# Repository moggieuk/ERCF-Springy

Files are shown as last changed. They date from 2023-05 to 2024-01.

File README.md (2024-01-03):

# ERCF-Springy (BETA-2)

ERCF "Springy" is a modification/upgrade to the ERCF v1.1 design.  One of the problems with ERCF is tuning the grip on the filament by swapping out different sized "top-hats" until sufficent grip is found.  This is a hassle and, although mostly works, the problem is that the flexible nature of the connection of filament blocks and the fact that the servo arm wears over time means that it isn't reliable.  Enter "Springy"...

Springy is a reworked Selector Cart (and ancillary components) with built in articulated sprung servo.  The whole servo assembly moves to ensure consistent pressure to grip the filament and works with a single "universal" top-hat.

## Beta 1 -> Beta 2 Changes:
<ol>
<li>Improved supports (gaps)
<li>Adjustment screw for spring (must always use the Spring_Cap.stl part). Obviously you need to add a threaded insert at the top of the spring hole -- careful you need a steady had to do this.
<li>Minor adjustment to servo mounting carts - they had a slightly lower resting position than desired
<li>The servo pivot is no longer two screws but a single M3x20.  It makes is slightly more difficult to assembly because you need to attach the encoder at the same time as securing the pivot for the servo. Idea from ERCF discord channel.
<li>STLs Updated: `[a]_Springy_Selector_Cart.stl`, `Spring_Cap.stl`, `Springy_MG90S_Servo_Mount.stl`, `Springy_Savox_Servo_Mount.stl`
</ol>

Also check out my other ERCF projects:
<ul>
<li>Happy Hare v3 software (https://github.com/moggieuk/ERCF-Software-V3)
<li>KlipperScreen Happy Hare Edition (https://github.com/moggieuk/KlipperScreen-Happy-Hare-Edition)
</ul>

Also, some folks have asked about making a donation to cover the cost of the all the coffee I'm drinking.  I'm not doing this for any financial reward but it you feel inclined a donation to PayPal https://www.paypal.me/moggieuk will certainly be spent making your life with ERCF more enjoyable.

Thank you!

## "Springy" Internals
This cross section reveals how Spring works.  The servo (both MG90S and Savox SH255mg are supported) pivots and provides about 2-3mm of movement.  The updated servo arm design aligns with the new universal top hat and ensures constant grip with varying distances and servo arm wear.

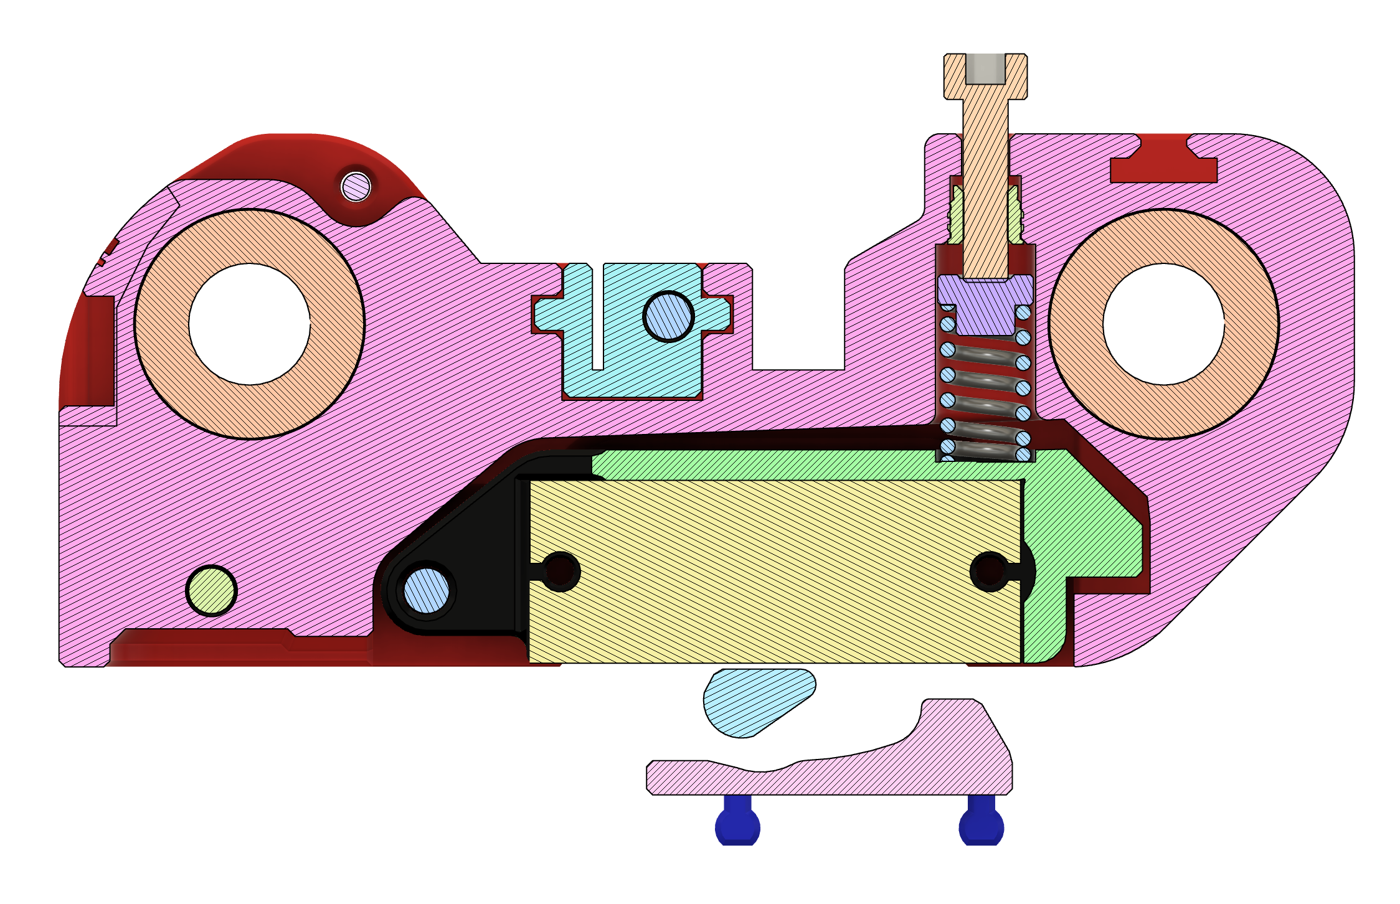
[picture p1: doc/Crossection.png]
ERCF Springy Cross Section


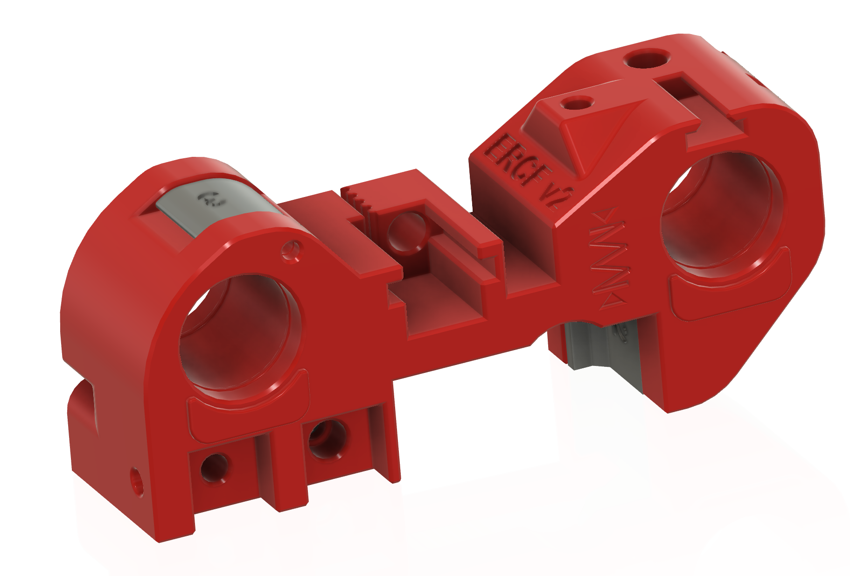
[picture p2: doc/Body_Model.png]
New Selector Arm Body


Other changes / notes:
<ul>
<li>The "Idler Block" at the end of the 8mm rods should be replaced to provide an enlarged pocket for servo movement.
<li>You must replace all your top-hats with the "universal" design supplied.
<li>The selector door has been strengthed in the hinge area and now locks with two 3x2mm magnets.
<li>Articulated servo mounts are provided for both the popular MG90S and Savox servo options.
<li>Springs from about 10mm to 15mm accomodated - cut it too long.  You do want the 1mm s/steel wire size though to provide the correct pressure.
</ul>

## Parts needed

### Printed Parts
In addition to the selector cart it is important to print and fit a new "Idler Block" to ensure the servo will not bind and wires have room to move. Also make sure you use the new top-hat and correct servo arm (the MG90S and Savox are different spline patterns!)

### Hardware
<ul>
<li>1x M3x20mm SHCS bolt for articulated servo pivot. This secures both the encoder and is the pivot for the articulated servo arm.
<li>1x 10mm - 15mm s/s compression spring.  This should be a 6mm diameter, 1mm wire compression spring.
<li>1x M3 heatset for the spring compression adjustment
<li>2x 3x2mm round neodymium magnets.  These are optional if you want the updated cover to lock shut.
<li>2x M2x8mm self tapping "servo" screws (these are the ones that were probably supplied with servo). Note the warning about too long screws below.

Here is the articulated servo mount showing the MG90S servo verion and a 12mm spring. The Savox mount is slightly different.

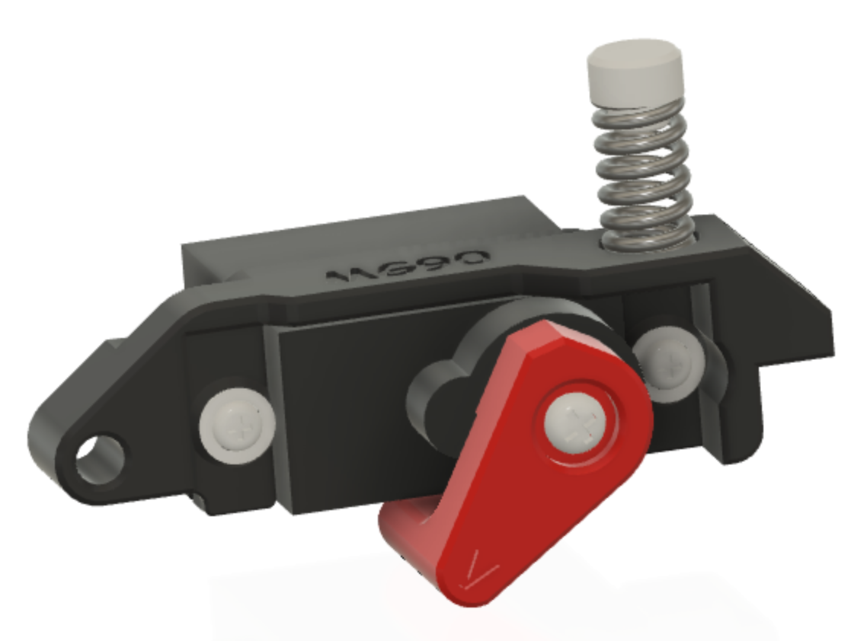
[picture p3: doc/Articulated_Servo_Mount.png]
MG90S Articulated Servo Mount


## Assembly

* Dissassembly: Remove the 6mm selector belt and separate the 8mm rods from the "Idle Block" end.  Remove the Encoder from the Selector Cart.  Remove the old Selector Cart from the 8mm rods.

* TO avoid clearance problems make sure to replace the Idle Block with the new one because is has a slightly enlarged cutout for servo.
  
* The servo mounts have break away suppports (MG90S has 4, Savox has 2) shown in grey below.  [Note: The print orientation is chosen to ensure strengh in the hinge area]. The M3 brass inserts are the same as the original with one exception.  The insert that forms the pivot for the servo should be set 1mm BELOW the surface.  The new STL has provision for this.

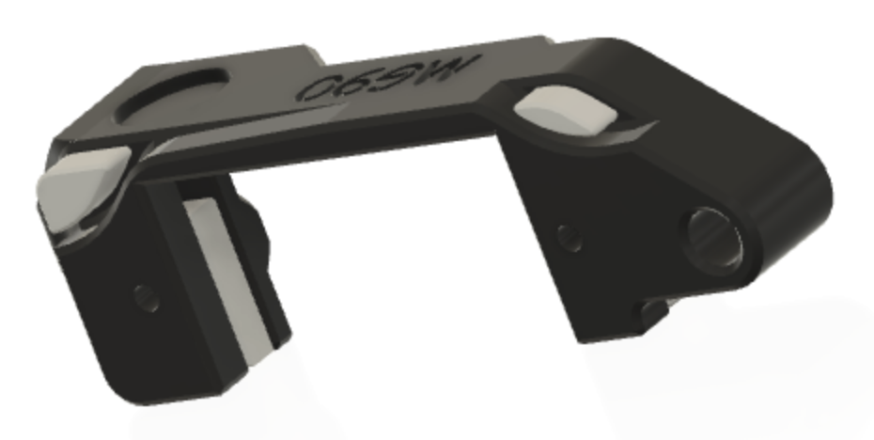
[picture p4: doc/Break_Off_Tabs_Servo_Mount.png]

  
* Fit the servo with two M2x6mm (or 8mm) self tapping screws.  IMPORTANT: Make sure the screws don't poke through to the other side. If they do, remove then and file then slightly before refitting. I found the screws supplied by the servo vendors fitted but others can be a little long.

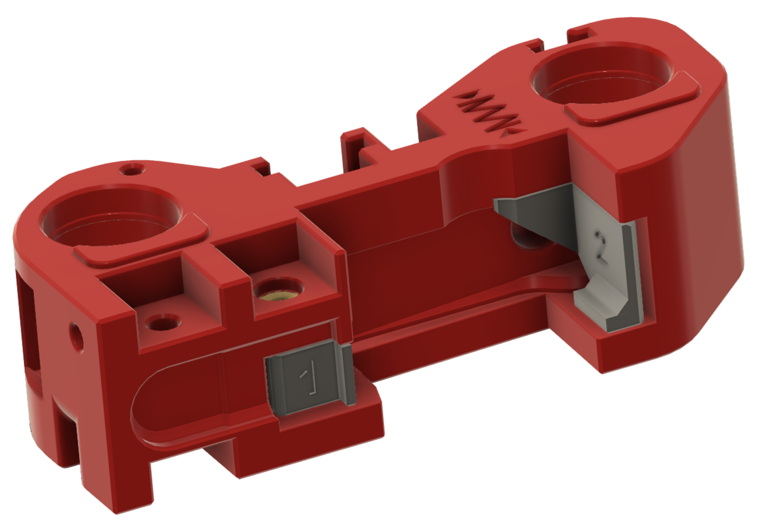
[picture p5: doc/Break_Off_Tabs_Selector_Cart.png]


* Break away the 3 numbered supports from the Selector Cart.

* Press a M3 heatset at the back of the spring hole.  Putting on the heatset on a M2 allen or small screwdriver will help guide it.  CAREFULLY with a steady hand, press the heatset into the base of the hole without deforming the surrounding plastic.

* Fit the spring and spring cap into the cart.  Insert the servo assemply spring side first then depress the pivot side and secure the servo pivot with a M3x20mm SHCS bolt (the same one that will later hold the encoder).

It should articulate similar to this video: (https://www.youtube.com/shorts/Brj2L9Y7NeA)

* Add back the encoder changing the one M3x8mm to a M3x20mm SHCS (fits into the other side of the brass insert shared with the servo pivot).
  
* Secure the servo wiring as shown in the picture.  The *small* loop will provide necessary free movement to prevent strain on the wire. **Don't fit the servo arm at this stage.**

Servo Wire 

* Reassemble ERCF and reconnect wiring.

* Replace all the Top Hats with the universal one supplied in this repo (they have a v2.0 printed on the top edge)

* Insert a 3x2mm magnet into the new stronger connector cover and corresponding hole on the selector cart
  
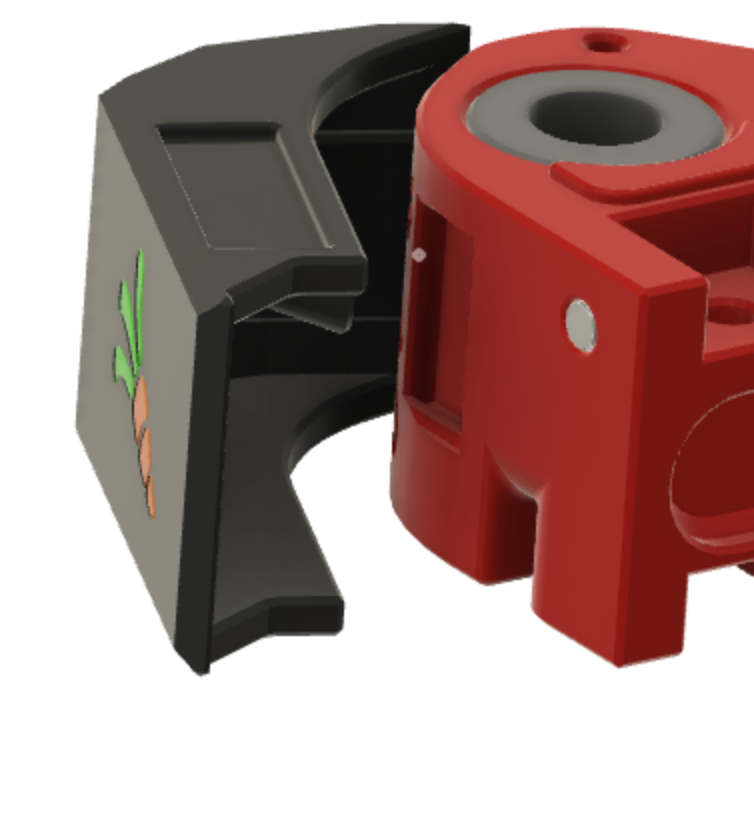
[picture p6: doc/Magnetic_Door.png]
Magnetic_Door
   

* Once ERCF is operational again, align the selector with one of the gates. Run `ERCF_SERVO_UP` to ensure the servo is in the up position.  Fit the new servo arm (Savox version has "S" on arm, MG90S is blank) on the spine that best holds the arm against the servo body (fine adjustments can be made later to the servo angle in `ercf_parameters.cfg`)

* Run `ERCF_SERVO_DOWN` or `ERCF_TEST_SERVO VALUE=xxx` to find the angle where the `V` on the servo arm aligns with the tiny `^` on the Top Hat.  This eliminates any judgement and represents the best location for the down position. **NOTE: the angle of movement is a little bit smaller than before, so don't assume your existing value is correct - test again carefully working up to the correct postion!
* For Happy Hare use:  `MMU_SERVO POS=down` or `MMU_SERVO ANGLE=xxx`

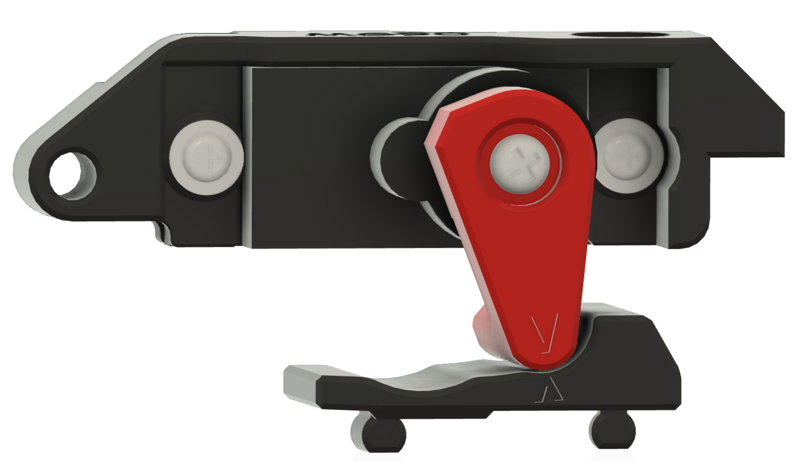
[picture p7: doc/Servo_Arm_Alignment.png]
Servo Arm Alignement


Now enjoy more reliable and hopefully less filament slippage.   Note: This removes one or two variables from your setup -- friction in the filament path can still lead to problems.

Good luck.  You can find me on Discord as `moggieuk#6538`

    (\_/)
    ( *,*)
    (")_(") ERCF Ready

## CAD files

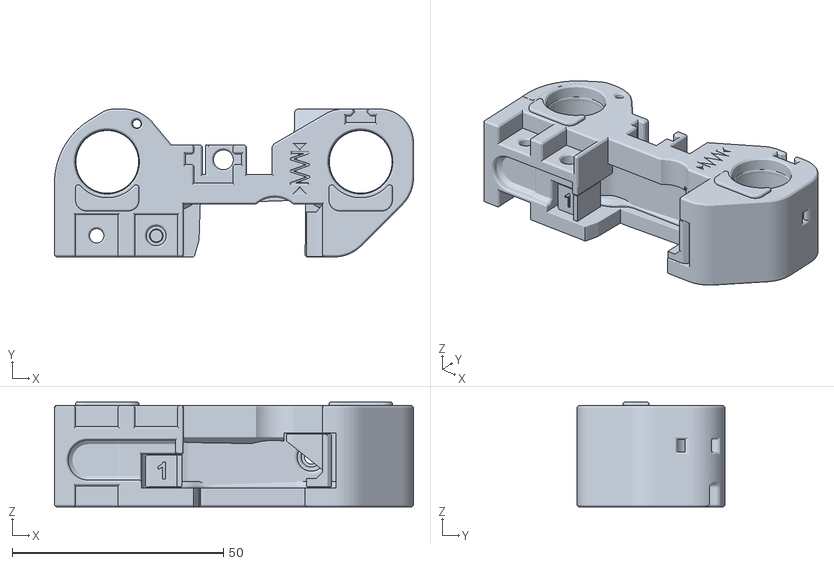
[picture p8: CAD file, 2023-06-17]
[a]_Springy_Selector_Cart.stl
85.0 x 35.0 x 24.8

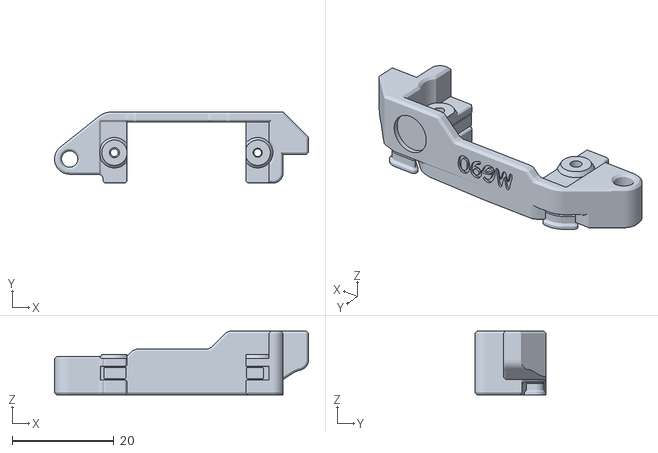
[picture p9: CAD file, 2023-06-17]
MG90S_Servo_Option/Springy_MG90S_Servo_Mount.stl
50.0 x 14.0 x 12.5

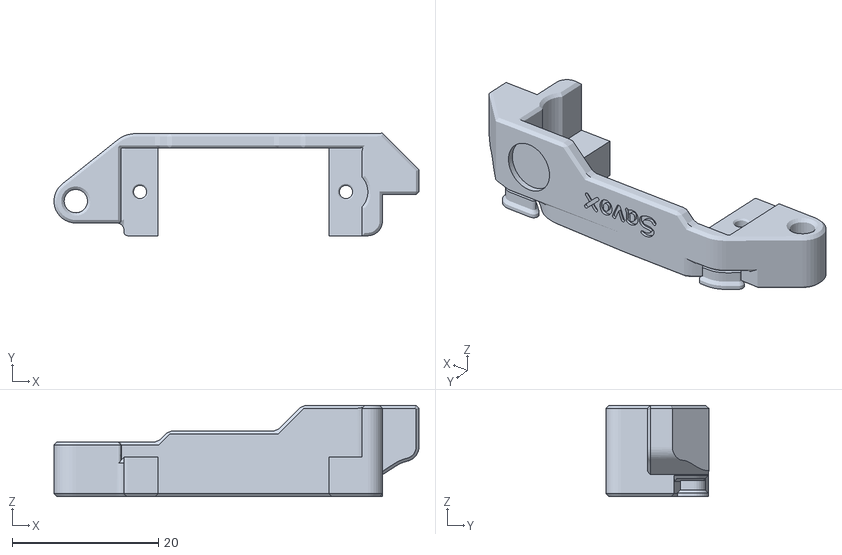
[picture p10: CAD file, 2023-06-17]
Savox_Servo_Option/Springy_Savox_Servo_Mount.stl
50.0 x 14.0 x 12.5

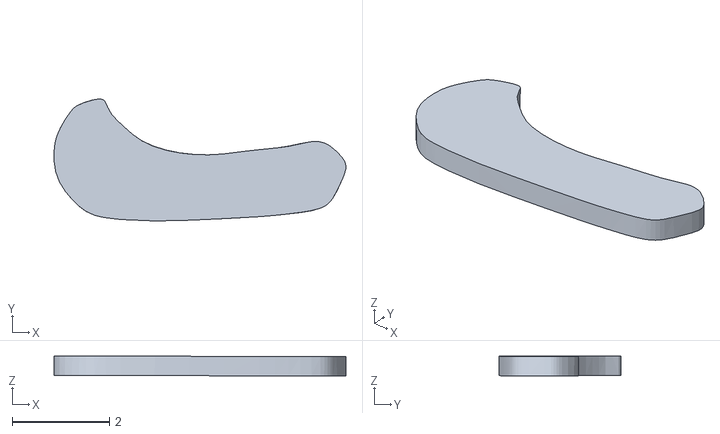
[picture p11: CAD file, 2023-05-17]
Selector_Door_Multicolor_Option/Selector_Door_Carrot_Leaf_1.stl
6.00 x 2.51 x 0.411

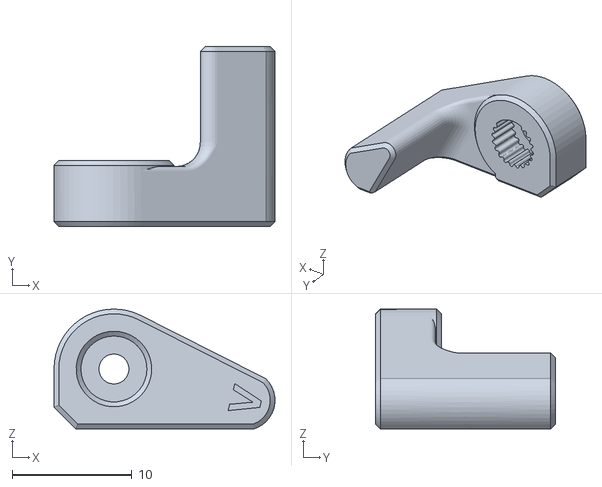
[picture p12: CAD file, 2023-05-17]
MG90S_Servo_Option/[a]_Servo_Arm_MG90S.stl
18.4 x 15.0 x 10.00

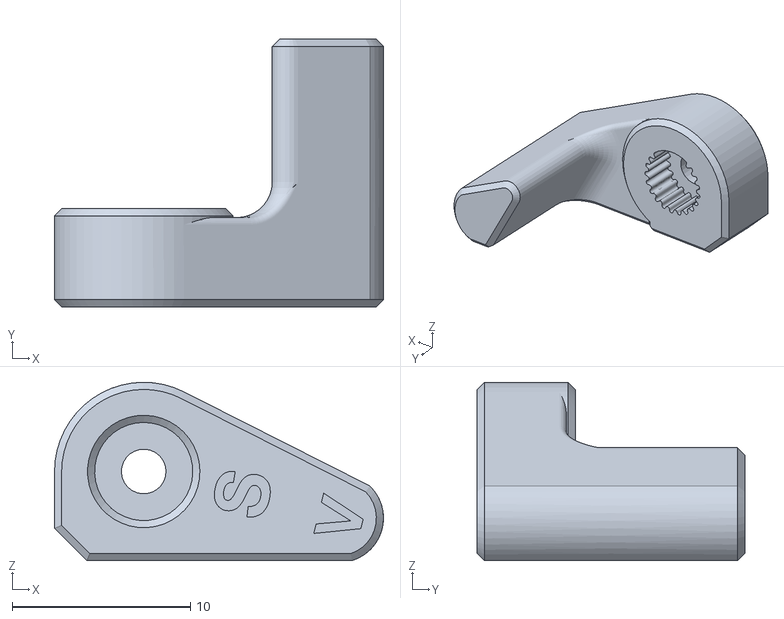
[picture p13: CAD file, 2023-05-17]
Savox_Servo_Option/[a]_Servo_Arm_Savox.stl
18.4 x 15.0 x 10.00

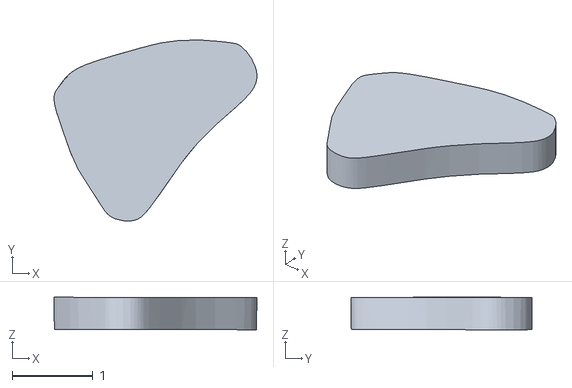
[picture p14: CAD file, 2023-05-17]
Selector_Door_Multicolor_Option/Selector_Door_Carrot_Body_3.stl
2.52 x 2.25 x 0.404

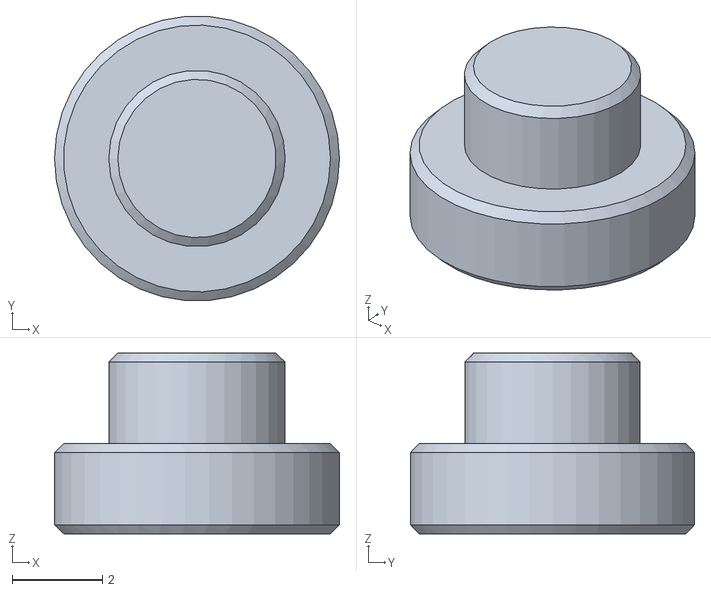
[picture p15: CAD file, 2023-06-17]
Spring_Cap.stl
6.30 x 6.28 x 4.00

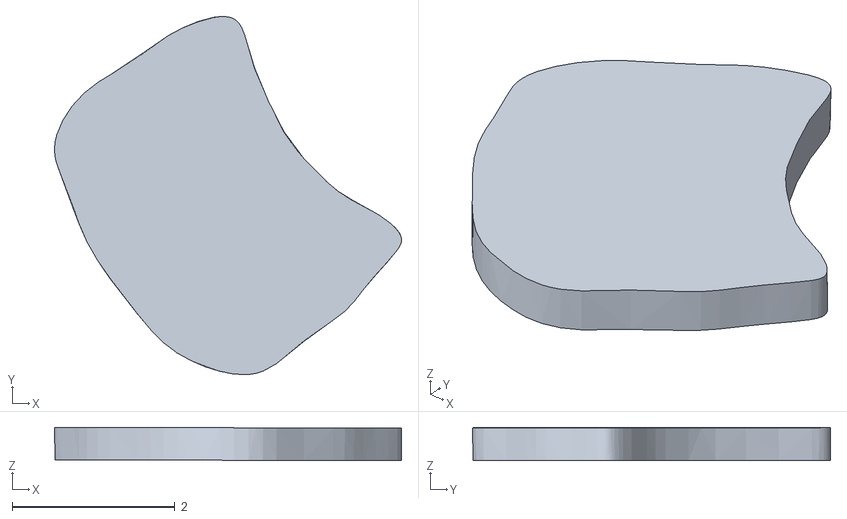
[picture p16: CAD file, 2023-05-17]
Selector_Door_Multicolor_Option/Selector_Door_Carrot_Body_1.stl
4.27 x 4.40 x 0.407

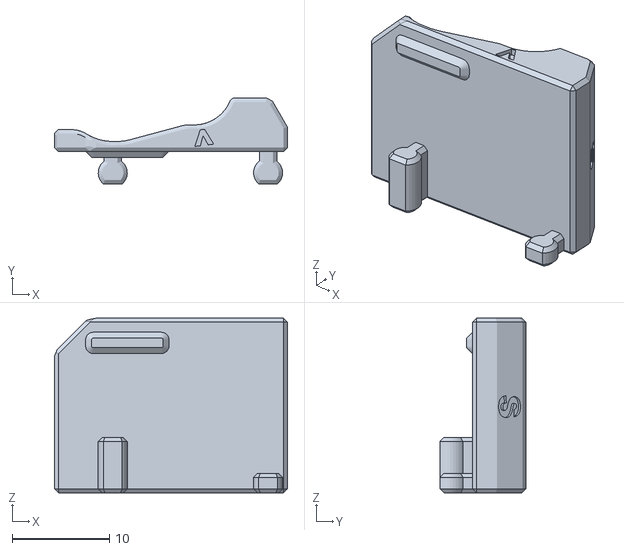
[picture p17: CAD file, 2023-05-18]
Springy_Top_Hat_xN.stl
24.0 x 8.85 x 18.0

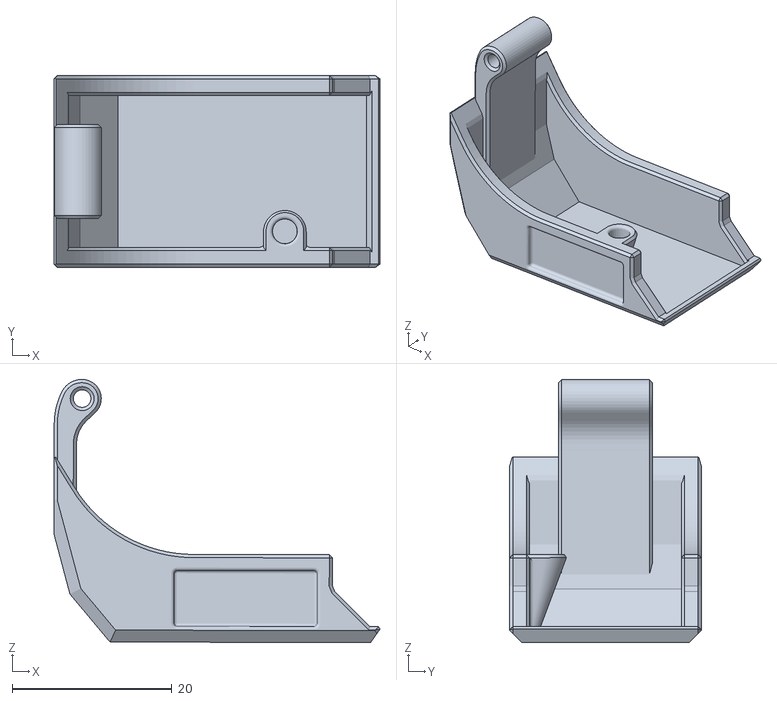
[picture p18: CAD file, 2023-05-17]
Selector_Door_Multicolor_Option/Springy_Selector_Door.stl
40.8 x 24.0 x 33.0

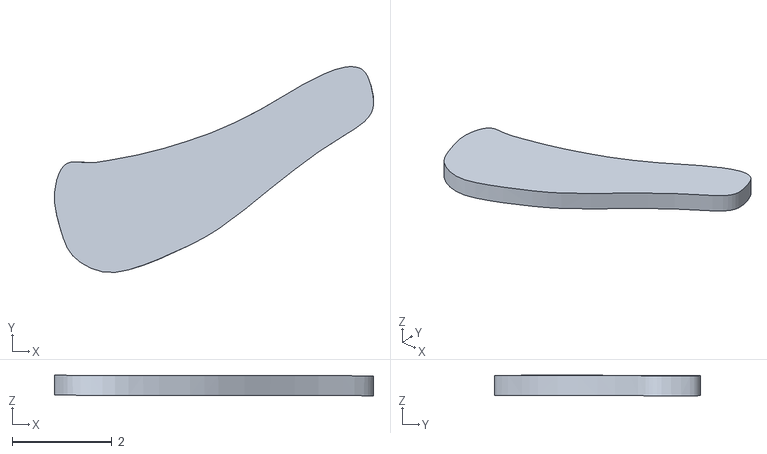
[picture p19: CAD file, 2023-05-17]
Selector_Door_Multicolor_Option/Selector_Door_Carrot_Leaf_2.stl
6.39 x 4.12 x 0.411

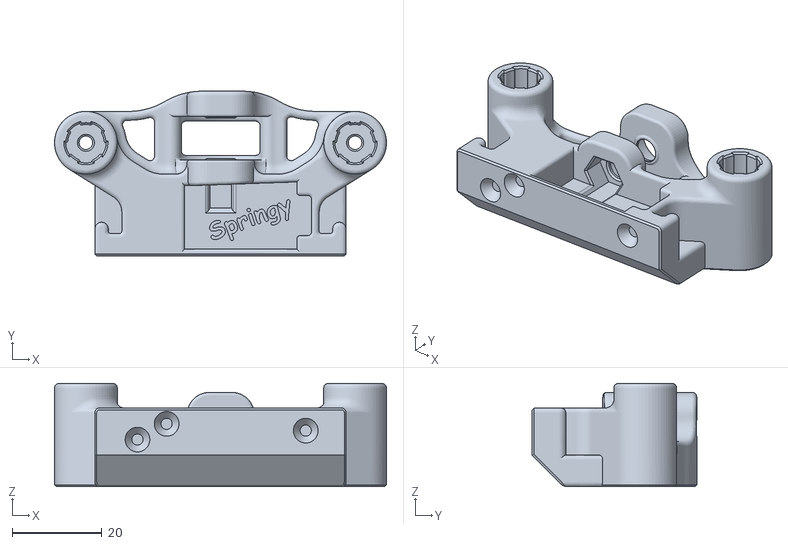
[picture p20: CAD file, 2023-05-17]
Springy_Idler_Block.stl
74.0 x 36.7 x 23.0

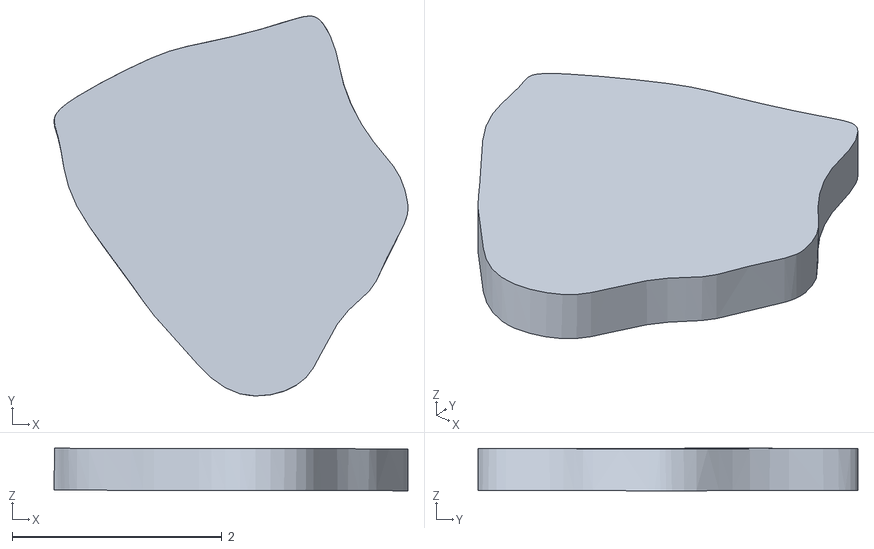
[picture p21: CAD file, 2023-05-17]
Selector_Door_Multicolor_Option/Selector_Door_Carrot_Body_2.stl
3.38 x 3.62 x 0.406

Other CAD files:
Selector_Door_Multicolor_Option/Selector_Door_Carrot_Leaf_3.stl

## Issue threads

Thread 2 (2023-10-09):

CAD files

mdvorak, 2023-10-09:
Hi, this looks really great, would you mind releasing CAD files? I'd like to do some minor modifications so I can use what I have already at home.

Thanks!

Side note: Is there a reason, why heatset insert for the spring screw is burried deep in the hole, instead simply putting it on top? It would be way easier to put it there.

ntchris, 2023-10-16:
CAD file would be nice, sure.
for the heat insert, my understanding is, if put it on top, it could be easily pushed out by the strong spring.  but like currently put in on the other side,  it's very strong, can resist the strong spring 's force upward.

mdvorak, 2023-10-16:
Good point, I don't think properly positioned heatinsert would actually fall out (especially when pushed a little further under surface), but I trust @moggieuk :)

todstelzer, 2024-09-22:
Just wanted to do a minor chance on the top hat and there are no CAD or STEP files...
Why?

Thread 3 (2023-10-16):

feature request to support 28mm length servo or even larger servo ?

ntchris, 2023-10-16:
feature request to support 28mm length servo or even larger servo ?
thanks.
I just printed and installed springy, currently it only supports 23mm servo.
I found that the 23mm micro servo sometimes cannot move to down position, or the spring put it back.
Maybe the 23mm micro servo is too weak, and cannot provide necessary force to push down.
There are some slightly larger 28mm length servo, should be better.
for example
https://www.aliexpress.com/item/1005003643468291.html?spm=a2g0o.cart.0.0.5cfb38dapkgguq&mp=1
17g metal gear

Maybe 33mm or  36mm or  40mm servo is too large to fit ?

without CAD files, other people are difficult to make mods for those, so maybe you could consider making those ?
thanks!

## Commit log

2023-05-17 added picture of servo wiring
2023-05-17 added pic of servo arm alignment
2023-05-17 Added picture of magnetic door
2023-05-18 Updated top hat design
    [Springy_Top_Hat_xN.stl]
2023-06-17 Beta 2 updates
    [12mm_Spring_Extension.stl, Spring_Cap.stl, Springy_MG90S_Servo_Mount.stl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]
